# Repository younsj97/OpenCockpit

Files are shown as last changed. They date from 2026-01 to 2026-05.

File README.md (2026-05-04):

# OpenCockpit
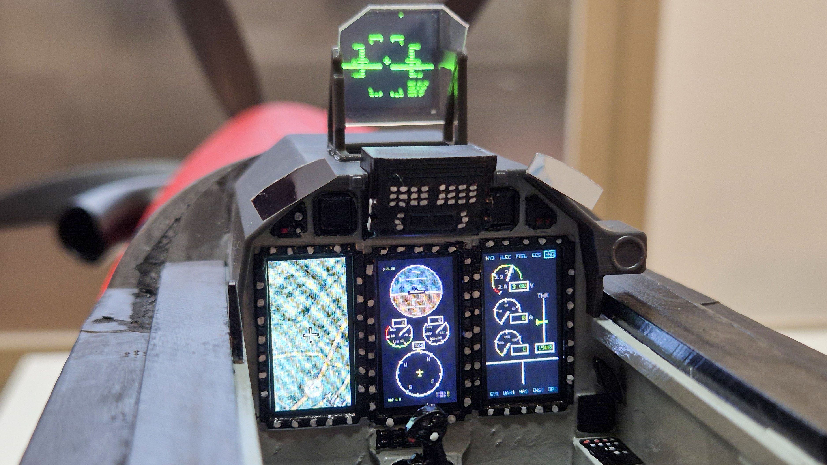
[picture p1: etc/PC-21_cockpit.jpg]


OpenCockpit is an open-source FPV cockpit display that uses a Raspberry Pi.  
It consists of working displays such as a HUD,MAP,MFD,INFO and it receives data from the flight controller(FC) to show live flight data in real time.

---

## Full Build Tutuorial
  - [English](https://vudev.notion.site/OpenCockpit-Build-Tutorial-3566ea6262ea80a49489f02d480d7f26?source=copy_link)
  - [한국어](https://vudev.notion.site/OpenCockpit-3566ea6262ea80b49948cab48c1eeefa?source=copy_link)

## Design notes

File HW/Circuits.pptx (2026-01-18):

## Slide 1

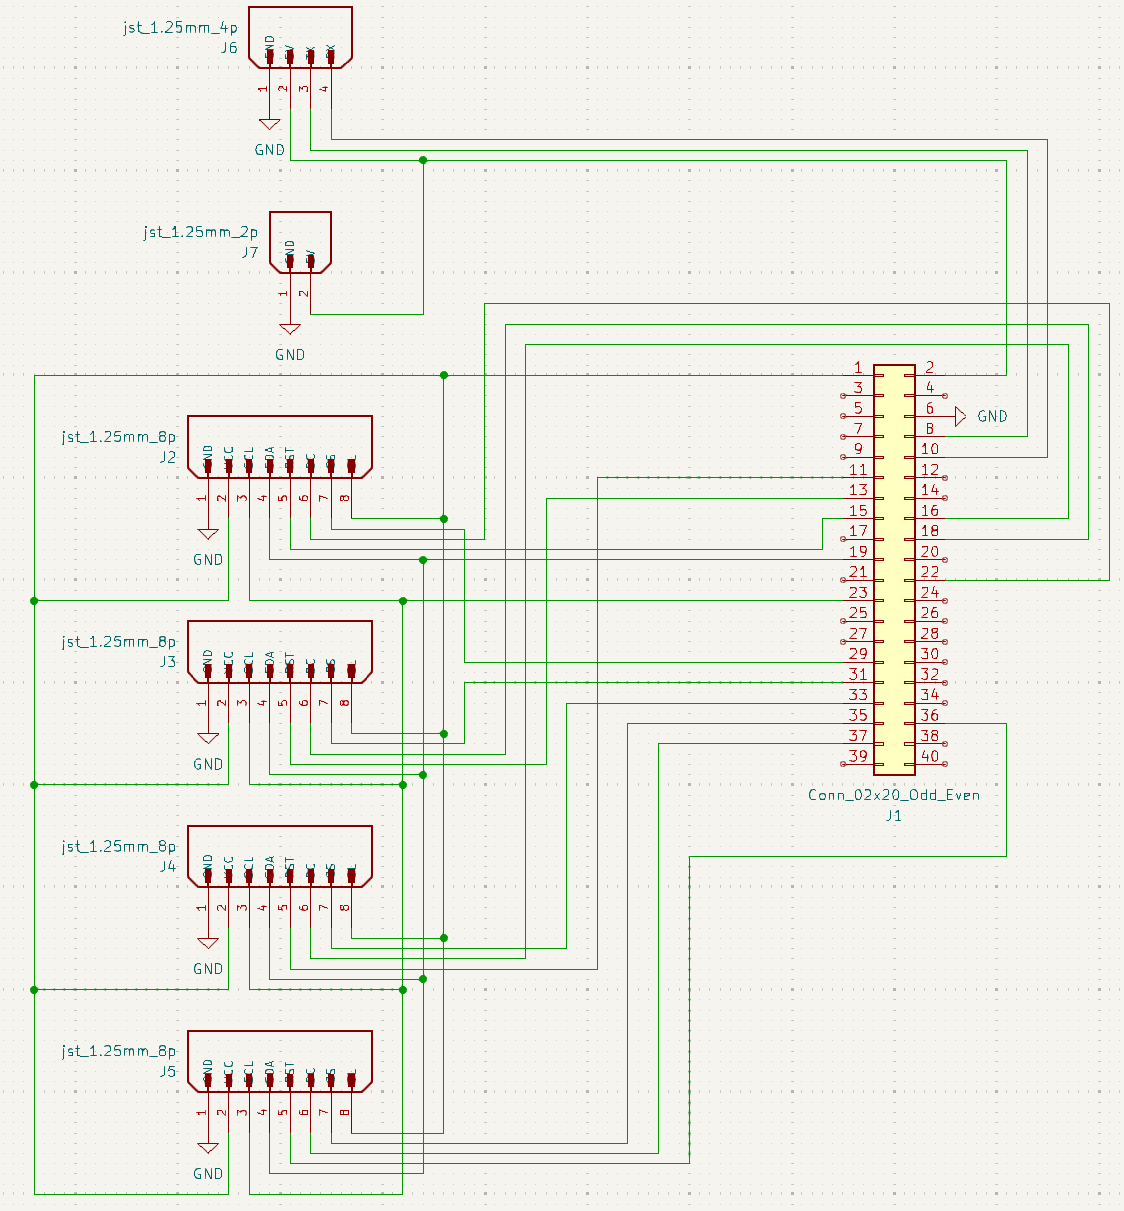
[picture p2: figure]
텍스트, 도표, 라인, 평행이(가) 표시된 사진 AI 생성 콘텐츠는 정확하지 않을 수 있습니다.

FC
- GND
- 5V
- TX : GPIO 14
- RX : GPIO 15

5V LED
- GND
- 5V

Display 1
- CS : GPIO 5
- DC : GPIO 25
- RST : GPIO 22

Display 2
- CS : GPIO 6
- DC : GPIO 24
- RST : GPIO 27

Display 3
- CS : GPIO 13
- DC : GPIO 23
- RST : GPIO 17

Display 4
- CS : GPIO 19
- DC : GPIO 26
- RST : GPIO 16

Display Common
- SCL : GPIO 11
- SDA : GPIO 10
- GND
- VCC : 3.3V
- BLK : 3.3V

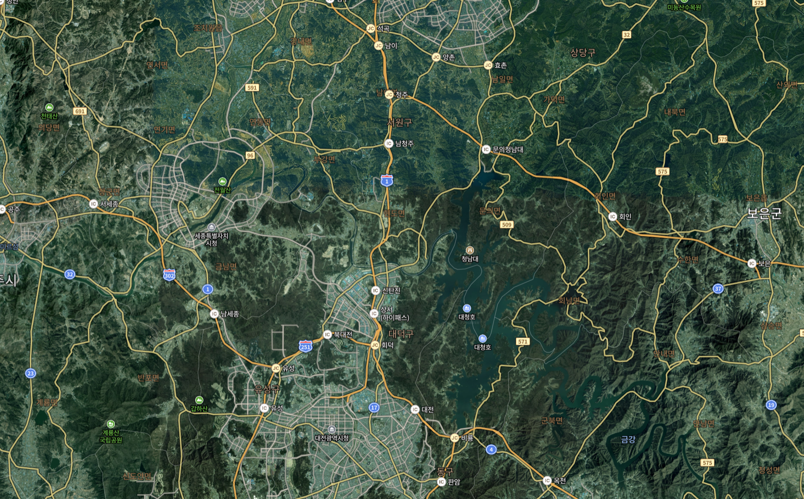
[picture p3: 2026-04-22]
OpenCockpit/map.png

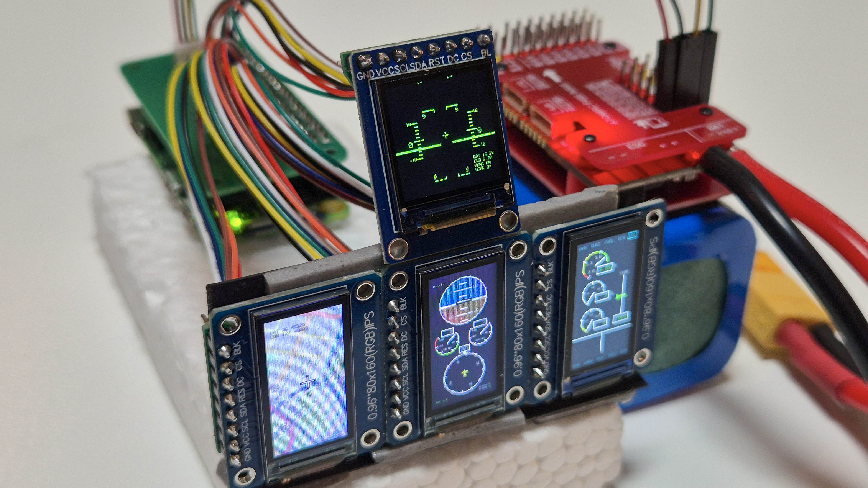
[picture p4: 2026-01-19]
etc/Prototype2.jpg

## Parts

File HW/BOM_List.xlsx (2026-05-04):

OpenCockpit BOM (4 Displays setup)
No | Module | Part name | Quantity | Link | Description
1 | Compute | Raspberry pi Zero 2W | 1
2 | Compute | Micro SD 16GB or 32GB | 1
3 | Compute | 3D print part - pillar | 4 | CAD file (https://naver.me/xwo9NUy8) | Print or Upload STL file and order at 3D print company like JLCPCB
4 | Compute | 3D print part - plate | 1 | CAD file (https://naver.me/xwo9NUy8) | Print or Upload STL file and order at 3D print company like JLCPCB
5 | Compute | 3D print part - plate_holder | 1 | CAD file (https://naver.me/xwo9NUy8) | Print or Upload STL file and order at 3D print company like JLCPCB
6 | Compute | PCB - Main | 1 | Github gerber file (https://github.com/younsj97/OpenCockpit/blob/main/HW/PCB/Main/Gerber/Main_gerber.zip) | Upload gerber.zip and order at PCB maker company like JLCPCB
7 | Compute | 2.54mm 2*20 header pin (straight) | 1 | aliexpress (https://ko.aliexpress.com/item/1005004790410396.html)
8 | Compute | 2.54mm 2*20 header socket (straight) | 1 | aliexpress (https://ko.aliexpress.com/item/1005006532505153.html)
9 | Compute | M2 4mm bolt (+) | 8 | aliexpress - H set (https://ko.aliexpress.com/item/1005010641850047.html?curPageLogUid=9umm03esJgh2)
10 | Compute | M2 6mm bolt (+) | 4 | aliexpress - H set (https://ko.aliexpress.com/item/1005010641850047.html?curPageLogUid=9umm03esJgh2)
11 | Compute | JST 1.25mm 4P male connector (straight) | 1 | aliexpress (https://ko.aliexpress.com/item/1005006027334406.html)
12 | Compute | JST 1.25mm 8P male connector (straight) | 4 | aliexpress (https://ko.aliexpress.com/item/1005006027334406.html)
13 | HUD | 3D print part - hud_frame | 1 | CAD file (https://naver.me/xwo9NUy8) | Upload STL file, select MJF and order at 3D print company like JLCPCB This part need heat resistance
14 | HUD | PCB - Display | 1 | Github gerber file (https://github.com/younsj97/OpenCockpit/blob/main/HW/PCB/Display/Gerber/Display_gerber.zip) | Upload gerber.zip and order at PCB maker company like JLCPCB
15 | HUD | 0.85inch SPI IPS Display | 1 | aliexpress (https://ko.aliexpress.com/item/1005008615538231.html)
16 | HUD | JST 1.25mm 8P male connector (straight) | 1 | aliexpress (https://ko.aliexpress.com/item/1005006027334406.html)
17 | HUD | Transparent PC board (0.5mm thickness) | 1 | aliexpress (https://ko.aliexpress.com/item/1005008956160925.html?curPageLogUid=eR10Q2TObDkt)
18 | HUD | HUD reflection film | 1 | aliexpress (https://ko.aliexpress.com/item/1005005996778139.html)
19 | HUD | LED (3W, 5V, Cold White 6500K) | 1 | aliexpress (https://ko.aliexpress.com/item/1005008762495460.html)
20 | HUD | 14*14*6mm heat sink | 1 | aliexpress (https://ko.aliexpress.com/item/1005003323689097.html)
21 | HUD | 1804 dc cooling fan | 1 | aliexpress (https://ko.aliexpress.com/item/1005008202270597.html?curPageLogUid=ZHip1rGnsSzf)
22 | HUD | M2 16mm bolt (Hex) | 2 | aliexpress – M2 set (https://ko.aliexpress.com/item/1005004833515587.html)
23 | HUD | Mirror Tape (for inside hud frame)
24 | Cockpit | 3D print part - cockpit_pcb_holder | 1 | CAD file (https://naver.me/xwo9NUy8) | Print or Upload STL file and order at 3D print company like JLCPCB
25 | Cockpit | 3D print part - cockpit_mirror | 2 | CAD file (https://naver.me/xwo9NUy8) | Print or Upload STL file and order at 3D print company like JLCPCB
26 | Cockpit | 3D print part - cockpit_hud_frame | 1 | CAD file (https://naver.me/xwo9NUy8) | Print or Upload STL file and order at 3D print company like JLCPCB
27 | Cockpit | 3D print part - cockpit_dash_top | 1 | CAD file (https://naver.me/xwo9NUy8) | Print or Upload STL file and order at 3D print company like JLCPCB
28 | Cockpit | 3D print part - cockpit_base | 1 | CAD file (https://naver.me/xwo9NUy8) | Print or Upload STL file and order at 3D print company like JLCPCB
29 | Cockpit | PCB - Display | 3 | Github gerber file (https://github.com/younsj97/OpenCockpit/blob/main/HW/PCB/Display/Gerber/Display_gerber.zip) | Upload gerber.zip and order at PCB maker company like JLCPCB
30 | Cockpit | 0.96inch SPI IPS Display | 3 | aliexpress (https://ko.aliexpress.com/item/32947890530.html)
31 | Cockpit | JST 1.25mm 8P male connector (straight) | 3 | aliexpress (https://ko.aliexpress.com/item/1005006027334406.html)
32 | Cockpit | Mirror Tape (for backmirror)
33 | Cockpit | Paint (Gray, Black, White, Red, Yellow)
34 | Cockpit | Paint brush or Spray
35 | Gimbal | 3D print part - servo_pan_mount_V2 | 1 | CAD file (https://naver.me/xwo9NUy8) | Print or Upload STL file and order at 3D print company like JLCPCB
36 | Gimbal | 3D print part - camera_mount_V2 | 1 | CAD file (https://naver.me/xwo9NUy8) | Print or Upload STL file and order at 3D print company like JLCPCB
37 | Gimbal | 3D print part - camera_mount_gear_servo_V2 | 1 | CAD file (https://naver.me/xwo9NUy8) | Print or Upload STL file and order at 3D print company like JLCPCB
38 | Gimbal | 3D print part - camera_mount_gear_cam_V2 | 1 | CAD file (https://naver.me/xwo9NUy8) | Print or Upload STL file and order at 3D print company like JLCPCB
39 | Gimbal | SG51R servo | 2 | aliexpress (https://ko.aliexpress.com/item/1005012040210051.html)
40 | Gimbal | M2 8mm bolt (Hex) | 2 | aliexpress – M2 set (https://ko.aliexpress.com/item/1005004833515587.html)
41 | Gimbal | M2 6mm bolt (Hex) | 1 | aliexpress – M2 set (https://ko.aliexpress.com/item/1005004833515587.html)
42 | Gimbal | M2 6mm bolt (+) | 4 | aliexpress - H set (https://ko.aliexpress.com/item/1005010641850047.html?curPageLogUid=9umm03esJgh2)
43 | Cable (Compute - HUD) | JST 1.25mm 2P male, female connector set | 1 | aliexpress (https://ko.aliexpress.com/item/4000898605030.html)
44 | Cable (Compute - Display) | JST 1.25mm 8P female-female cable - same side (20cm or 30cm) | 4 | aliexpress (https://ko.aliexpress.com/item/1005005682847096.html)
45 | Cable (Compute - FC) | JST 1.25mm 4p female-2.54mm dupont female 4p cable | 1 | aliexpress (https://ko.aliexpress.com/item/1005005454071973.html)
46 | VTX mount | 3D print part - vtx_mount_b | 1 | CAD file (https://naver.me/xwo9NUy8) | Print or Upload STL file and order at 3D print company like JLCPCB
47 | VTX mount | 3D print part - vtx_mount_t | 1 | CAD file (https://naver.me/xwo9NUy8) | Print or Upload STL file and order at 3D print company like JLCPCB
48 | VTX mount | 2507 dc cooling fan | 1 | aliexpress - 5V (https://ko.aliexpress.com/item/32842948804.html?curPageLogUid=3ky2oZHZCGRO)
49 | VTX mount | M2 washer | 4 | aliexpress (https://ko.aliexpress.com/item/1005008318320472.html?curPageLogUid=tBg2x1SC5EdW)
50 | VTX mount | M2 12mm bolt (Hex) | 4 | aliexpress – M2 set (https://ko.aliexpress.com/item/1005004833515587.html)
51 | VTX mount | M2 6mm bolt (+) | 4 | aliexpress - H set (https://ko.aliexpress.com/item/1005010641850047.html?curPageLogUid=9umm03esJgh2)
52 | Canopy | Tinted Canopy | 2 | aliexpress (https://ko.aliexpress.com/item/1005003056730961.html) | Since defects occur often, additional purchase of spares recommended
53 | Canopy | M2 4mm bolt (Lock Canopy) | 4 | aliexpress - H set (https://ko.aliexpress.com/item/1005010641850047.html?curPageLogUid=9umm03esJgh2)
54 | Canopy | M2 washer (Lock Canopy) | 4 | aliexpress (https://ko.aliexpress.com/item/1005008318320472.html?curPageLogUid=tBg2x1SC5EdW)
55 | Canopy | M2 Insert nut (Lock Canopy) | 4 | aliexpress - M2 (https://ko.aliexpress.com/item/33006298977.html?curPageLogUid=d6aYO9im1OoY)
56 | Tool | Soldering tools
57 | Tool | Screwdriver (PH1)
58 | Tool | Hex Screwdriver or Hex Key (H1.3)
59 | Tool | CA Glue
60 | Tool | Epoxy Glue (like B-7000)
61 | Tool | Knife
62 | Tool | Diagonal cutter
63 | Tool | Heat-shrink tube
64 | Head Tracking | XF Headtracker | 1 | aliexpress (https://ko.aliexpress.com/item/1005008237528042.html)
65 | Head Tracking | 3.5mm TRS male-male cable | 1 | aliexpress - 2m (https://ko.aliexpress.com/item/1005003175350504.html?curPageLogUid=w8i7AHVZHj2B)

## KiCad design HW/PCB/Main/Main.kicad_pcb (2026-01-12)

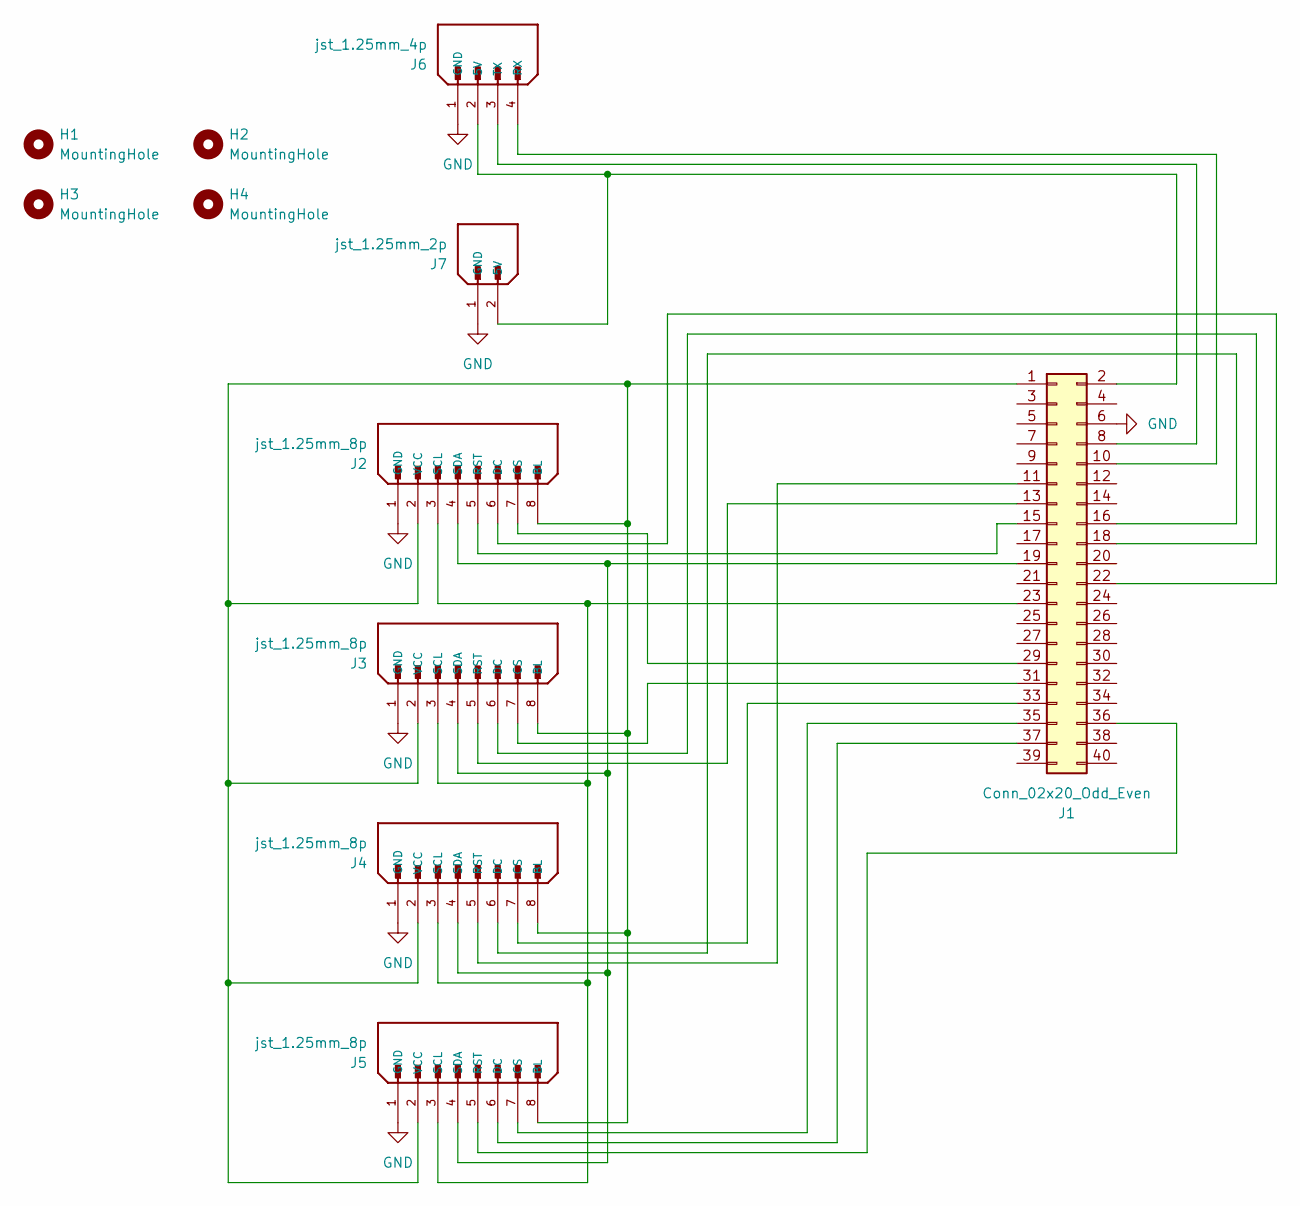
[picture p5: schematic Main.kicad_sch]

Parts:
H1, H2, H3, H4: MountingHole; MountingHole_2.2mm_M2
J1: Conn_02x20_Odd_Even; PinSocket_2x20_P2.54mm_Vertical
J2, J3, J4, J5: jst_1.25mm_8p
J6: jst_1.25mm_4p
J7: jst_1.25mm_2p

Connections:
GND: J1.6 (GND), J2.1 (GND), J3.1 (GND), J4.1 (GND), J5.1 (GND), J6.1 (GND), J7.1 (GND)
unnamed: J1.1 (3.3V), J2.2 (VCC), J2.8 (BL), J3.2 (VCC), J3.8 (BL), J4.2 (VCC), J4.8 (BL), J5.2 (VCC), J5.8 (BL)
unnamed: J1.29 (DP1_CS), J2.7 (CS)
unnamed: J1.22 (DP1_DC), J2.6 (DC)
unnamed: J1.15 (DP1_RST), J2.5 (RST)
unnamed: J1.31 (DP2_CS), J3.7 (CS)
unnamed: J1.18 (DP2_DC), J3.6 (DC)
unnamed: J1.13 (DP2_RST), J3.5 (RST)
unnamed: J1.33 (DP3_CS), J4.7 (CS)
unnamed: J1.16 (DP3_DC), J4.6 (DC)
unnamed: J1.11 (DP3_RST), J4.5 (RST)
unnamed: J1.35 (DP4_CS), J5.7 (CS)
unnamed: J1.37 (DP4_DC), J5.6 (DC)
unnamed: J1.36 (DP4_RST), J5.5 (RST)
unnamed: J1.8, J6.3 (TX)
unnamed: J1.10, J6.4 (RX)
unnamed: J1.23 (SCK), J2.3 (SCL), J3.3 (SCL), J4.3 (SCL), J5.3 (SCL)
unnamed: J1.19 (SDA), J2.4 (SDA), J3.4 (SDA), J4.4 (SDA), J5.4 (SDA)
unnamed: J1.2 (5V), J6.2 (5V), J7.2 (5V)

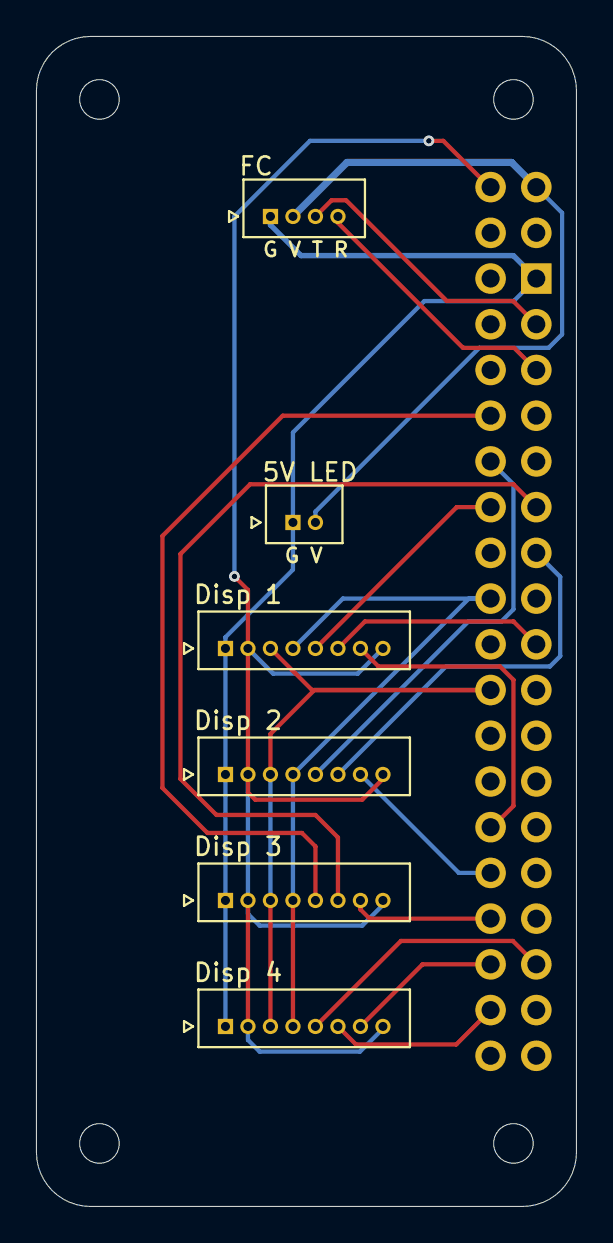
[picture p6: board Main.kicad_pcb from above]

Board: 2 copper layers, 30.0 x 65.0 mm, 11 parts (0 on the bottom side), 19 nets.

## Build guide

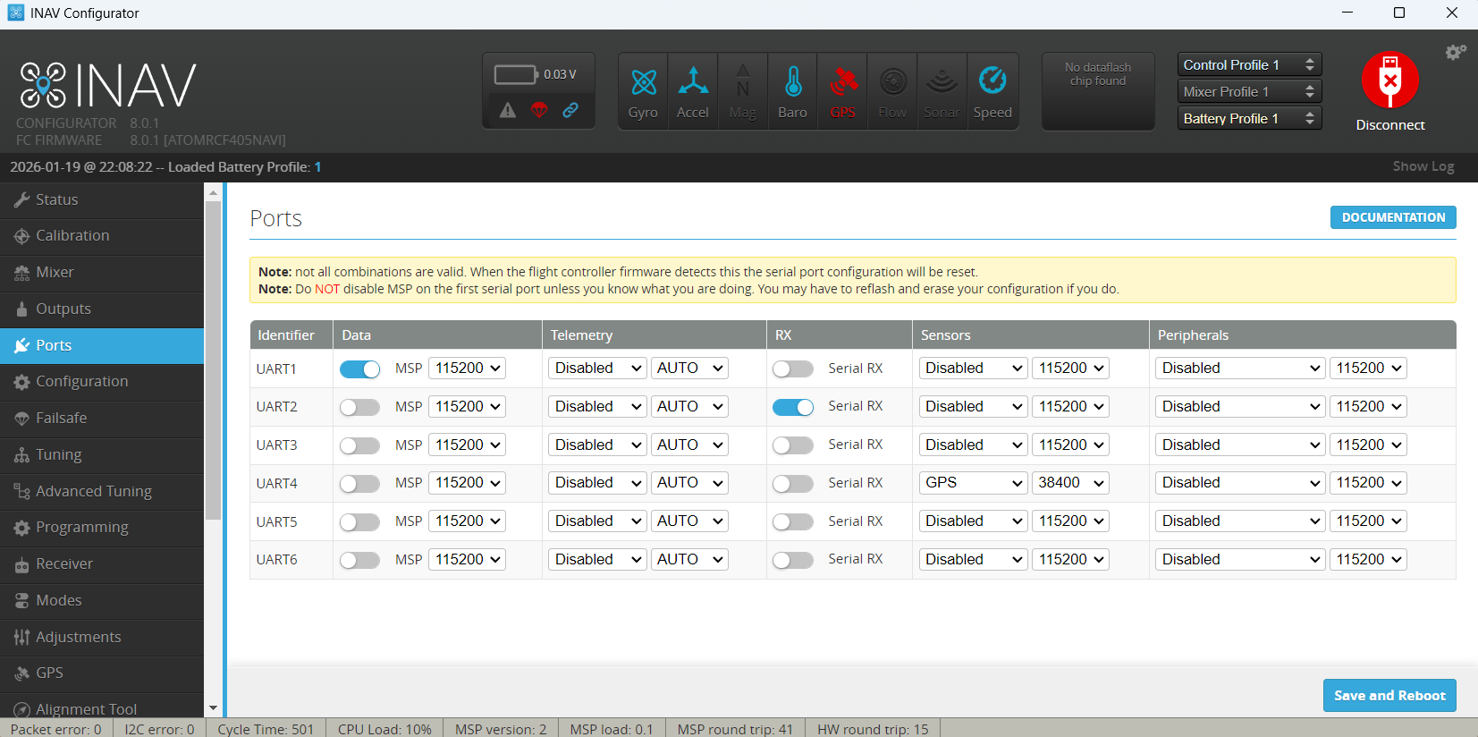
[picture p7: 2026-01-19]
etc/INAV_ports_setup.png

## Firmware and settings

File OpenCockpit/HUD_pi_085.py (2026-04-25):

import MSP_Read_pi

import board
import digitalio
import busio
import math
import pygame
import time
import numpy as np

import adafruit_rgb_display.st7735 as ST7735


# Display hardware configuration (used by main.py to initialize)
DISPLAY_CONFIG = {
    "driver": "ST7735",
    "width": 128,
    "height": 128,
    "rotation": 180,
    "x_offset": 2,
    "y_offset": 1,
    "invert": True
}


# ---------------------------- GUI Configuration ----------------------------------------

# Display settings
WIDTH, HEIGHT = 128, 128
FPS = 30
PITCH_MOVE_SCALE = 10 # pixels moved per degree of pitch (horizontal line spacing)
ALT_MOVE_SCALE = 2 # pixels moved per altitude (vertical line spacing)
SPD_MOVE_SCALE = 2 # pixels moved per speed unit (vertical line spacing)


# ---------------------------- Base Configuration ----------------------------------------

# Set center point
CENTER_X, CENTER_Y = WIDTH / 2, HEIGHT / 2

# Set colors
GREEN = (0, 255, 0)
BLACK = (0, 0, 0)

# Initialize Pygame
pygame.init()
screen = pygame.display.set_mode((WIDTH, HEIGHT))
clock = pygame.time.Clock()

# Load fonts
font = pygame.font.Font("/boot/firmware/OpenCockpit/ViperDisplay-Bold.ttf",8)
font_mid = pygame.font.Font("/boot/firmware/OpenCockpit/ViperDisplay-Bold.ttf",6)
font_small = pygame.font.Font("/boot/firmware/OpenCockpit/ViperDisplay-Bold.ttf",5)


# ---------------------------- FC data Variables (for testing) ----------------------------------------
pitch = 0.0             # deg
roll = 0.0              # deg
yaw = 0.0               # deg
v_speed = 21.0          # vertical speed
alt = 256               # altitude
speed_3d = 94           # 3d speed
sats = 10               # GPS satellites count
course = 123            # GPS course
vbat = 16.2             # voltage
current = 12.5          # ampere
home_dist = 512         # meter
home_dir = 30           # degree


# ---------------------------- GUI rotation functions ----------------------------------------

# Line rotation function - for horizon lines
def rotate_point(x, y, angle_deg):
    rad = math.radians(angle_deg)
    cos_a = math.cos(rad)
    sin_a = math.sin(rad)
    return (
        x * cos_a - y * sin_a,
        x * sin_a + y * cos_a
    )

# Text rotation function - for pitch degree texts
def draw_text_rotated(text, x, y, angle_deg, align="left", font=font_mid):
    surf = font.render(text, True, GREEN)
    rotated_surf = pygame.transform.rotate(surf, angle_deg)
    rotated_rect = rotated_surf.get_rect()
    if align == "right":
        rotated_rect.topright = (x, y)
    else:
        rotated_rect.topleft = (x, y)
    screen.blit(rotated_surf, rotated_rect)

# Draw text function
def draw_text(text, x, y, align="left", font=font):
    surf = font.render(text, True, GREEN)
    rect = surf.get_rect()
    if align == "right":
        rect.topright = (x, y)
    else:
        rect.topleft = (x, y)
    screen.blit(surf, rect)


# ---------------------------- Draw horizon lines & pitch degree texts functions ----------------------------------------
def draw_horizon_lines(pitch, roll, yaw):
    for deg in range(-180, 180, 5):
        offset_y = (deg - pitch) * PITCH_MOVE_SCALE

        if abs(offset_y) > HEIGHT:
            continue

        # Set half line length based on degree
        if deg == 0:
            length_half = 140
        else:
            length_half = 22

        # Calculate Y position before rotation with pitch offset
        y = CENTER_Y + offset_y

        # Line endpoints before rotation
        x1, y1 = -length_half, 0
        x2, y2 = length_half, 0

        # Define endpoints before rotation in screen coordinates
        ux1, uy1 = CENTER_X + x1 + yaw, y + y1
        ux2, uy2 = CENTER_X + x2 + yaw, y + y2

        # Translate points to origin for rotation
        dx1, dy1 = ux1 - CENTER_X, uy1 - CENTER_Y
        dx2, dy2 = ux2 - CENTER_X, uy2 - CENTER_Y

        # Rotate according to roll
        rdx1, rdy1 = rotate_point(dx1, dy1, -roll)
        rdx2, rdy2 = rotate_point(dx2, dy2, -roll)

        # Endpoints after rotation
        x1_after_rotate, y1_after_rotate = CENTER_X + rdx1, CENTER_Y + rdy1
        x2_after_rotate, y2_after_rotate = CENTER_X + rdx2, CENTER_Y + rdy2

        # Calculate total line length after rotation
        dx = x2_after_rotate - x1_after_rotate
        dy = y2_after_rotate - y1_after_rotate
        L = math.hypot(dx, dy)

        if L == 0:
            continue

        # Calculate center point after rotation
        x_center_after_rotate = x1_after_rotate + dx / 2
        y_center_after_rotate = y1_after_rotate + dy / 2

        # Set middle gaps size at center of lines
        mid_gap = 8
        ox = dx * mid_gap / L
        oy = dy * mid_gap / L

        # Draw lines and markers - below horizon
        if deg > 0:

            # Set small gap(gap in line) size
            small_gap = 1.6
            ox_small = dx * small_gap / L
            oy_small = dy * small_gap / L

            # Set small gap(gap in line) positions
            small_gap1_position = (1 / 9)
            small_gap2_position = (1 / 4)
            small_gap3_position = 1 - small_gap2_position
            small_gap4_position = 1 - small_gap1_position

            p1x = x1_after_rotate + dx * small_gap1_position # left small gap 1 center position
            p1y = y1_after_rotate + dy * small_gap1_position # left small gap 1 center position
            p2x = x1_after_rotate + dx * small_gap2_position # left small gap 2 center position
            p2y = y1_after_rotate + dy * small_gap2_position # left small gap 2 center position
            p3x = x1_after_rotate + dx * small_gap3_position # right small gap 1 center position
            p3y = y1_after_rotate + dy * small_gap3_position # right small gap 1 center position
            p4x = x1_after_rotate + dx * small_gap4_position # right small gap 2 center position
            p4y = y1_after_rotate + dy * small_gap4_position # right small gap 2 center position

            # Draw first line (between left end and left small gap 1)
            pygame.draw.line(screen, GREEN, (x1_after_rotate, y1_after_rotate), (p1x - ox_small, p1y - oy_small), 1)
            # Draw second line (between left small gap 1 and left small gap 2)
            pygame.draw.line(screen, GREEN, (p1x + ox_small, p1y + oy_small), (p2x - ox_small, p2y - oy_small), 1)
            # Draw second line (between left small gap 2 and middle gap)
            pygame.draw.line(screen, GREEN, (p2x + ox_small, p2y + oy_small), (x_center_after_rotate - ox, y_center_after_rotate - oy), 1)
            # Draw third line (between middle gap and right small gap 1)
            pygame.draw.line(screen, GREEN, (x_center_after_rotate + ox, y_center_after_rotate + oy), (p3x - ox_small, p3y - oy_small), 1)
            # Draw third line (between right small gap 1 and right small gap 2)
            pygame.draw.line(screen, GREEN, (p3x + ox_small, p3y + oy_small), (p4x - ox_small, p4y - oy_small), 1)
            # Draw fourth line (between right small gap 2 and right end)
            pygame.draw.line(screen, GREEN, (p4x + ox_small, p4y + oy_small), (x2_after_rotate, y2_after_rotate), 1)
            
            # Set marker length and direction (perpendicular to horizon line)
            marker_length = 2.4
            perp_x = -dy / L
            perp_y = dx / L
            marker_line_width = 1
            
            # Draw markers at left side of middle gap
            marker_left_x = x_center_after_rotate - ox # left side of middle gap
            marker_left_y = y_center_after_rotate - oy # left side of middle gap
            marker_left_end_x = marker_left_x - marker_length * perp_x # End point of left marker
            marker_left_end_y = marker_left_y - marker_length * perp_y # End point of left marker
            pygame.draw.line(screen, GREEN, (marker_left_x, marker_left_y), (marker_left_end_x, marker_left_end_y), marker_line_width)
            
            # Draw markers at right side of middle gap
            marker_right_x = x_center_after_rotate + ox # right side of middle gap
            marker_right_y = y_center_after_rotate + oy # right side of middle gap
            marker_right_end_x = marker_right_x - marker_length * perp_x # End point of right marker
            marker_right_end_y = marker_right_y - marker_length * perp_y # End point of right marker
            pygame.draw.line(screen, GREEN, (marker_right_x, marker_right_y), (marker_right_end_x, marker_right_end_y), marker_line_width)
            
        # Draw lines and markers - above horizon
        elif deg < 0:
            
            # Draw first line (left side of middle gap)
            pygame.draw.line(screen, GREEN, (x1_after_rotate, y1_after_rotate), (x_center_after_rotate - ox, y_center_after_rotate - oy), 1)
            # Draw second line (right side of middle gap)
            pygame.draw.line(screen, GREEN, (x_center_after_rotate + ox, y_center_after_rotate + oy), (x2_after_rotate, y2_after_rotate), 1)
            
            # Set marker length and direction (perpendicular to horizon line)
            marker_length = 3
            perp_x = -dy / L
            perp_y = dx / L
            marker_line_width = 1
            
            # Draw markers at left side of middle gap
            marker_left_x = x_center_after_rotate - ox # left side of middle gap
            marker_left_y = y_center_after_rotate - oy # left side of middle gap
            marker_left_end_x = marker_left_x + marker_length * perp_x # End point of left marker
            marker_left_end_y = marker_left_y + marker_length * perp_y # End point of left marker
            pygame.draw.line(screen, GREEN, (marker_left_x, marker_left_y), (marker_left_end_x, marker_left_end_y), marker_line_width)
            
            # Draw markers at right side of middle gap
            marker_right_x = x_center_after_rotate + ox # right side of middle gap
            marker_right_y = y_center_after_rotate + oy # right side of middle gap
            marker_right_end_x = marker_right_x + marker_length * perp_x # End point of right marker
            marker_right_end_y = marker_right_y + marker_length * perp_y # End point of right marker
            pygame.draw.line(screen, GREEN, (marker_right_x, marker_right_y), (marker_right_end_x, marker_right_end_y), marker_line_width)
        else:
            # deg == 0
            # Draw line (left side of middle gap)
            pygame.draw.line(screen, GREEN, (x1_after_rotate, y1_after_rotate), (x_center_after_rotate - ox, y_center_after_rotate - oy), 2)
            # Draw line (right side of middle gap)
            pygame.draw.line(screen, GREEN, (x_center_after_rotate + ox, y_center_after_rotate + oy), (x2_after_rotate, y2_after_rotate), 2)


        # Draw pitch degree texts (except 0 degree) - below horizon
        if deg > 0:

            # Set text position offsets
            text_offset_x = 1
            text_offset_y = -8

            # Draw left end deg value text
            text_x_left = x1_after_rotate - text_offset_x * (dx / L) - text_offset_y * (dy / L)
            text_y_left = y1_after_rotate - text_offset_x * (dy / L) + text_offset_y * (dx / L)
            text_angle = math.degrees(math.atan2(dy, dx))
            draw_text_rotated(f"{deg}", int(text_x_left), int(text_y_left), -text_angle, align="left")
            
            # Draw right end deg value text
            text_x_right = x2_after_rotate + text_offset_x * (dx / L) - text_offset_y * (dy / L)
            text_y_right = y2_after_rotate + text_offset_x * (dy / L) + text_offset_y * (dx / L)
            draw_text_rotated(f"{deg}", int(text_x_right), int(text_y_right), -text_angle, align="right")
        
        # Draw pitch degree texts (except 0 degree) - above horizon
        if deg < 0:
            # Set text position offsets
            text_offset_x = 1
            text_offset_y = -2

            # Draw left end deg value text
            text_x_left = x1_after_rotate - text_offset_x * (dx / L) + text_offset_y * (dy / L)
            text_y_left = y1_after_rotate - text_offset_x * (dy / L) - text_offset_y * (dx / L)
            text_angle = math.degrees(math.atan2(dy, dx))
            draw_text_rotated(f"{-deg}", int(text_x_left), int(text_y_left), -text_angle, align="left")
            
            # Draw right end deg value text
            text_x_right = x2_after_rotate + text_offset_x * (dx / L) + text_offset_y * (dy / L)
            text_y_right = y2_after_rotate + text_offset_x * (dy / L) - text_offset_y * (dx / L)
            draw_text_rotated(f"{-deg}", int(text_x_right), int(text_y_right), -text_angle, align="right")


# ---------------------------- Draw altitude & 3d speed lines and texts functions ----------------------------------------

# Draw altitude line function
def draw_altmeter(alt):
    alt_center_x = CENTER_X + 33
    alt_center_y = CENTER_Y
    altmeter_display_range = 20

    # Draw center line
    pygame.draw.line(screen, GREEN, (alt_center_x - 5, alt_center_y), (alt_center_x - 2, alt_center_y), 1)

    # Set small scale for altitude ticks
    alt_scale = 2

    # Draw altitude ticks (small ticks)
    for alt_tick in range(int(alt) - 60, int(alt) + 61, alt_scale):
        if alt_tick % 10 == 0:
            continue  # Scale of 10 will be drawn later
            
        # Calculate alt_tick position (centered around current alt)
        offset = (alt - alt_tick) * ALT_MOVE_SCALE
        
        # Set screen Y position
        tick_y = alt_center_y + offset
        
        # Check range
        if abs(offset) > altmeter_display_range:
            continue

        # Draw small ticks
        pygame.draw.line(screen, GREEN, (alt_center_x + 3, tick_y), (alt_center_x, tick_y), 1)
    
    # Draw altitude ticks (10s ticks with text)
    start_alt = (int(alt) // 10) * 10 - 60
    for alt_tick in range(start_alt, int(alt) + 70, 10):
        # Calculate alt_tick position (centered around current alt)
        offset = (alt - alt_tick) * ALT_MOVE_SCALE
        
        # Set screen Y position
        tick_y = alt_center_y + offset

        # Check range
        if abs(offset) > altmeter_display_range:
            continue

        # Draw 10s ticks with longer line
        pygame.draw.line(screen, GREEN, (alt_center_x + 7, tick_y), (alt_center_x, tick_y), 1)
        
        # Draw altitude value text (skip center value to avoid overlapping with altitude number)
        if not (tick_y < alt_center_y + 10 and tick_y > alt_center_y - 3):
            draw_text(f"{alt_tick}", alt_center_x + 7, int(tick_y - 2), align="left", font=font_small)

# Draw 3d speed line function
def draw_speedmeter(speed_3d):
    speed_center_x = CENTER_X - 33
    speed_center_y = CENTER_Y
    speed_display_range = 20

    # Draw center line
    pygame.draw.line(screen, GREEN, (speed_center_x + 2, speed_center_y), (speed_center_x + 5, speed_center_y), 1)

    # Set small scale for speed ticks
    speed_scale = 2

    # Draw speed ticks (small ticks)
    for speed_tick in range(int(speed_3d) - 60, int(speed_3d) + 61, speed_scale):
        if speed_tick % 10 == 0:
            continue  # Scale of 10 will be drawn later
            
        # Calculate speed_tick position (centered around current speed)
        offset = (speed_3d - speed_tick) * SPD_MOVE_SCALE
        
        # Set screen Y position
        tick_y = speed_center_y + offset
        
        # Check range
        if abs(offset) > speed_display_range:
            continue

        # Draw small ticks
        pygame.draw.line(screen, GREEN, (speed_center_x - 3, tick_y), (speed_center_x, tick_y), 1)
    
    # Draw speed ticks (10s ticks with text)
    start_speed = (int(speed_3d) // 10) * 10 - 60
    for speed_tick in range(start_speed, int(speed_3d) + 70, 10):
        # Calculate speed_tick position (centered around current speed)
        offset = (speed_3d - speed_tick) * ALT_MOVE_SCALE
        
        # Set screen Y position
        tick_y = speed_center_y + offset

        # Check range
        if abs(offset) > speed_display_range:
            continue

        # Draw 10s ticks with longer line
        pygame.draw.line(screen, GREEN, (speed_center_x - 7, tick_y), (speed_center_x, tick_y), 1)
        
        # Draw speed value text (skip center value to avoid overlapping with speed number)
        if not (tick_y < speed_center_y + 10 and tick_y > speed_center_y - 3):
            draw_text(f"{speed_tick}", speed_center_x - 7, int(tick_y - 2), align="right", font=font_small)


# ---------------------------- Draw Crosshiar function ----------------------------------------

# Draw center crosshair function
def draw_center_crosshair():
    crosshair_size = 3
    crosshair_mid_gap = 1.6
    crosshair_line_width = 1
    pygame.draw.line(screen, GREEN, (CENTER_X - crosshair_size, CENTER_Y), (CENTER_X - crosshair_mid_gap, CENTER_Y), crosshair_line_width)
    pygame.draw.line(screen, GREEN, (CENTER_X + crosshair_mid_gap, CENTER_Y), (CENTER_X + crosshair_size, CENTER_Y), crosshair_line_width)
    pygame.draw.line(screen, GREEN, (CENTER_X, CENTER_Y - crosshair_size), (CENTER_X, CENTER_Y - crosshair_mid_gap), crosshair_line_width)
    pygame.draw.line(screen, GREEN, (CENTER_X, CENTER_Y + crosshair_mid_gap), (CENTER_X, CENTER_Y + crosshair_size), crosshair_line_width)


# ---------------------------- Render all lines and texts functions ----------------------------------------

# Render HUD lines and texts function
def render_hud(pitch, roll, yaw, v_speed, alt, speed_3d, sats, course, vbat, current, home_dist, home_dir):
    
        # Clear screen
        screen.fill(BLACK)

        # Draw horizon lines
        draw_horizon_lines(pitch, roll, yaw = 0)

        # Draw center crosshair
        draw_center_crosshair()

        # Draw 3D speed meter (left side of HUD)
        draw_speedmeter(speed_3d)

        # 3D speed text (left side of HUD)
        draw_text(f"{int(speed_3d)}", CENTER_X - 42, CENTER_Y, align="right")

        # Draw altitude meter (right side of HUD)
        draw_altmeter(alt)

        # Altitude text (right side of HUD)
        draw_text(f"{int(alt)}", CENTER_X + 42, CENTER_Y, align="left")

        # Info texts (bottom right side of HUD)
        draw_text(f"BAT {vbat:.1f}V", CENTER_X + 31, CENTER_Y + 30, align="left", font=font_small)
        draw_text(f"CUR {current:.1f}A", CENTER_X + 31, CENTER_Y + 35, align="left", font=font_small)
        draw_text(f"HOME {home_dist}m", CENTER_X + 31, CENTER_Y + 40, align="left", font=font_small)
        draw_text(f"HOME {home_dir}°", CENTER_X + 31, CENTER_Y + 45, align="left", font=font_small)


#---------------------------- Setup for Threading environment & SPI Display ----------------------------------------

# Get MSP data snapshot safely (Prevent data flow interruption in multi-threading environment)
def get_msp_snapshot(msp):
    with msp.data_lock:
        return dict(msp.data)

# RGB888 to RGB565 conversion function
def rgb888_to_rgb565(raw, width, height):
    arr = np.frombuffer(raw, dtype=np.uint8).reshape((height, width, 3))

    # Flip screen vertically (enable with reflect HUD screen)
    #arr = arr[::-1, :, :]

    r = (arr[:, :, 0] >> 3).astype(np.uint16)
    g = (arr[:, :, 1] >> 2).astype(np.uint16)
    b = (arr[:, :, 2] >> 3).astype(np.uint16)

    rgb565 = (r << 11) | (g << 5) | b

    rgb565_be = rgb565.byteswap()

    return rgb565_be.tobytes()


#---------------------------- Main loop with MSP data ----------------------------------------

# Main loop with MSP data
def main(MSP_data):
    while True:
        clock.tick(FPS)

        snap = get_msp_snapshot(MSP_Read_pi)

        pitch = snap["pitch"] if snap["pitch"] is not None else 0.0
        roll  = snap["roll"]  if snap["roll"]  is not None else 0.0
        yaw   = snap["yaw"]   if snap["yaw"]   is not None else 0.0
        alt = snap["alt"] if snap["alt"] is not None else 0.0
        v_speed = snap["v_speed"] if snap["v_speed"] is not None else 0.0
        speed_3d = snap["speed_3d"] if snap["speed_3d"] is not None else 0.0
        sats = snap["sats"] if snap["sats"] is not None else 0
        course = snap["course"] if snap["course"] is not None else 0
        vbat = snap["vbat"] if snap["vbat"] is not None else 0.0
        current = snap["current"] if snap["current"] is not None else 0.0
        home_dist = snap["home_dist"] if snap["home_dist"] is not None else 0
        home_dir = snap["home_dir"] if snap["home_dir"] is not None else 0

        # Render HUD
        render_hud(pitch, roll, yaw, v_speed, alt, speed_3d, sats, course, vbat, current, home_dist, home_dir)

        # Get pygame surface data
        raw = pygame.image.tostring(screen, "RGB")
        # Convert RGB888 to RGB565
        buf = rgb888_to_rgb565(raw, WIDTH, HEIGHT)
        # ST7735 Display update (block write)
        disp_7735._block(0, 0, WIDTH - 1, HEIGHT - 1, buf)
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

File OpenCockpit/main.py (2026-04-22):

import threading
import time
import sys
import pygame
import board
import digitalio
import busio
import numpy as np

# 모듈 임포트
import MSP_Read_pi
import HUD_pi_114
import HUD_pi_085
import MFD_pi_096
import MAP_pi_096
import INFO_pi_096

import adafruit_rgb_display.st7735 as ST7735
import adafruit_rgb_display.st7789 as ST7789

# ==========================================================
# [Setting] Select display and module
# If you enter only the display you want to use, the rest is automatically disabled
# ==========================================================
# [설정] 디스플레이와 모듈을 선택하세요
# 원하는 디스플레이만 입력하면 나머지는 자동으로 비활성화됩니다.
# ==========================================================
# Example(예시)
# {
#   "Display_2": "MFD_0.96",
#   "Display_3": "MAP_0.96",
# } 
# ==========================================================
SELECTED_DISPLAYS = {
    "Display_1": "HUD_0.85",
    "Display_2": "MAP_0.96",
    "Display_3": "MFD_0.96",
    "Display_4": "INFO_0.96",
}
# ==========================================================


# Define SPI pinmap of Raspberry Pi
DISPLAY_HARDWARE_MAP = {
    "Display_1": {"cs": board.D5,  "dc": board.D25, "rst": board.D22},
    "Display_2": {"cs": board.D6,  "dc": board.D24, "rst": board.D27},
    "Display_3": {"cs": board.D13, "dc": board.D23, "rst": board.D17},
    "Display_4": {"cs": board.D19, "dc": board.D26, "rst": board.D16}
}

# Mapping module file names to entered module names
MODULE_MAP = {
    "HUD_1.14": HUD_pi_114,
    "HUD_0.85": HUD_pi_085,
    "MFD_0.96": MFD_pi_096,
    "MAP_0.96": MAP_pi_096,
    "INFO_0.96" : INFO_pi_096
}

# Set framerate config
HIGH_FPS = 30
LOW_FPS = 15

# Init SPI bus
spi = busio.SPI(board.SCK, MOSI=board.MOSI)

PIN_OBJECTS = {}

for disp_id, pins in DISPLAY_HARDWARE_MAP.items():
    cs  = digitalio.DigitalInOut(pins["cs"])
    dc  = digitalio.DigitalInOut(pins["dc"])
    rst = digitalio.DigitalInOut(pins["rst"])

    cs.direction  = digitalio.Direction.OUTPUT
    dc.direction  = digitalio.Direction.OUTPUT
    rst.direction = digitalio.Direction.OUTPUT

    cs.value  = True   # deselect
    dc.value  = False  # default
    rst.value = True   # keep reset released

    PIN_OBJECTS[disp_id] = {
        "cs": cs,
        "dc": dc,
        "rst": rst
    }

# Map of driver name to constructor
DRIVER_MAP = {
    "ST7735": ST7735.ST7735R,
    "ST7789": ST7789.ST7789
}

# Initializes the appropriate display for the hardware pin 
# based on the ID and module object received from SELECTED_DISPLAYS.
def init_display(display_id, module_obj):

    mod_cfg = module_obj.DISPLAY_CONFIG

    driver_name = mod_cfg.get("driver")
    constructor = DRIVER_MAP.get(driver_name)
    
    if constructor is None:
        raise RuntimeError(f"Unsupported driver: {driver_name}")

    # Set SPI pins (based on DISPLAY_HARDWARE_MAP)
    pins = PIN_OBJECTS[display_id]
    cs  = pins["cs"]
    dc  = pins["dc"]
    rst = pins["rst"]

    # force rst reset
    rst.value = False
    time.sleep(0.05)
    rst.value = True
    time.sleep(0.05)

    # Make display configs dictionary
    display_kwargs = {
        "spi": spi,
        "cs": cs,
        "dc": dc,
        "rst": rst,
        "width": mod_cfg.get("width"),
        "height": mod_cfg.get("height"),
        "rotation": mod_cfg.get("rotation"),
        "x_offset": mod_cfg.get("x_offset"),
        "y_offset": mod_cfg.get("y_offset"),
        "baudrate": 52000000
    }

    # Add invert factor when driver is ST7735
    if driver_name == "ST7735":
        display_kwargs["invert"] = mod_cfg.get("invert")
    
    disp = constructor(**display_kwargs)
    
    return disp

# RGB888 to RGB565 conversion function
def rgb888_to_rgb565(raw, width, height):
    arr = np.frombuffer(raw, dtype=np.uint8).reshape((height, width, 3))
    r = (arr[:, :, 0] >> 3).astype(np.uint16)
    g = (arr[:, :, 1] >> 2).astype(np.uint16)
    b = (arr[:, :, 2] >> 3).astype(np.uint16)
    rgb565 = (r << 11) | (g << 5) | b
    return rgb565.byteswap().tobytes()

# Get MSP data snapshot safely (Prevent data flow interruption in multi-threading environment)
def get_msp_snapshot():
    with MSP_Read_pi.data_lock:
        return dict(MSP_Read_pi.data)

# Thread target: render and draw display loop for each module
def display_loop(module, disp, width, height, fps):

    # Get pygame screen elements from each module
    module.screen = pygame.Surface((width, height))
    module.WIDTH, module.HEIGHT = width, height
    module.CENTER_X, module.CENTER_Y = width / 2, height / 2

    clock = pygame.time.Clock()

    # Render fixed components
    if hasattr(module, "render_mfd_fixed"):
        module.render_mfd_fixed()
    if hasattr(module, "render_info_fixed"):
        module.render_info_fixed()

    # Render dynamic components
    while True:
        clock.tick(fps)

        snap = get_msp_snapshot()

        # Extract fields with None fallback
        pitch = snap["pitch"] if snap["pitch"] is not None else 0.0
        roll  = snap["roll"]  if snap["roll"]  is not None else 0.0
        yaw   = snap["yaw"]   if snap["yaw"]   is not None else 0.0
        alt = snap["alt"] if snap["alt"] is not None else 0.0
        lat = snap["lat"] if snap["lat"] is not None else 36.45325
        lon = snap["lon"] if snap["lon"] is not None else 127.40603
        v_speed = snap["v_speed"] if snap["v_speed"] is not None else 0.0
        speed_3d = snap["speed_3d"] if snap["speed_3d"] is not None else 0.0
        sats = snap["sats"] if snap["sats"] is not None else 0
        course = snap["course"] if snap["course"] is not None else 0
        vbat = snap["vbat"] if snap["vbat"] is not None else 0.0
        current = snap["current"] if snap["current"] is not None else 0.0
        rssi = snap["rssi"] if snap["rssi"] is not None else 0.0
        throttle = snap["throttle"] if snap["throttle"] is not None else 0.0
        home_dist = snap["home_dist"] if snap["home_dist"] is not None else 0
        home_dir = snap["home_dir"] if snap["home_dir"] is not None else 0

        # Call rendering function by module
        if hasattr(module, "render_hud"):
            module.render_hud(pitch, roll, yaw, v_speed, alt, speed_3d, sats, course, vbat, current, home_dist, home_dir)
        elif hasattr(module, "render_mfd_dynamic"):
            module.render_mfd_dynamic(pitch, roll, yaw, v_speed, alt, speed_3d, sats, course, vbat, current, home_dist, home_dir)
        elif hasattr(module, "render_map"):
            module.render_map(yaw, v_speed, alt, lat, lon, speed_3d, sats, course, vbat, current, home_dist, home_dir)
        elif hasattr(module, "render_info_dynamic"):
            module.render_info_dynamic(vbat, current, rssi, throttle)
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
